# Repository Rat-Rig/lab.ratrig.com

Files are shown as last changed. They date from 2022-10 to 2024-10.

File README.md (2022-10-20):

# lab.ratrig.com

# What is the Rat Rig Lab?
Through the Rat Rig Lab, we share designs and ideas which fall into the following categories:

## Official Mods
Sometimes we need a particular part which we design internally. An example being an IEC socket mount which bolts onto an aluminium 3030 extrusion. These parts are developed but do not belong to any particular product we provide.

This section will serve as a home to all of those designs, so that members of the community can use them if they find the need. We provide both STEP and STL files for each, ready to be printed or added into your own mods.

## Upcoming & Prototype Products
From prototypes early in the development process, to designs nearing to official announcement and release. This section houses projects which we aim to make commercially available.

## Non-commercial Designs
The research and development process does not always result in a product that is commercially viable at the time. This section contains those designs which did not become a product we currently sell, but that we may revisit in the future.

We share and document these designs, as well as the ideas and timelines behind them in this section. You can also find CAD models and the bill of materials should someone wish to build the design for themselves.

### Discontinued Products
Products are sometimes superseded with new and improved versions, or simply no longer sell and are discontinued. Here you can find products which fall into these categories. We provide the CAD models, and the full bill of materials, so that these designs are never lost.

## CAD Repository
Most of the components we use in our CAD models are modelled in-house. This section is a repository of those CAD models which are available for the community to use in their own designs.

By using our official models, you can be assured that the design you create will match the product you can purchase.

# License
  

Unless specified otherwise, all content published on the Rat Rig Lab is licensed under the <a rel="license" href="http://creativecommons.org/licenses/by-nc-sa/4.0/">Creative Commons Attribution-NonCommercial-ShareAlike 4.0 International License</a>

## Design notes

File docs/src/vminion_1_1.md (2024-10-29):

---
title: V-Minion 1.1 Alpha
hide:
  - navigation
---
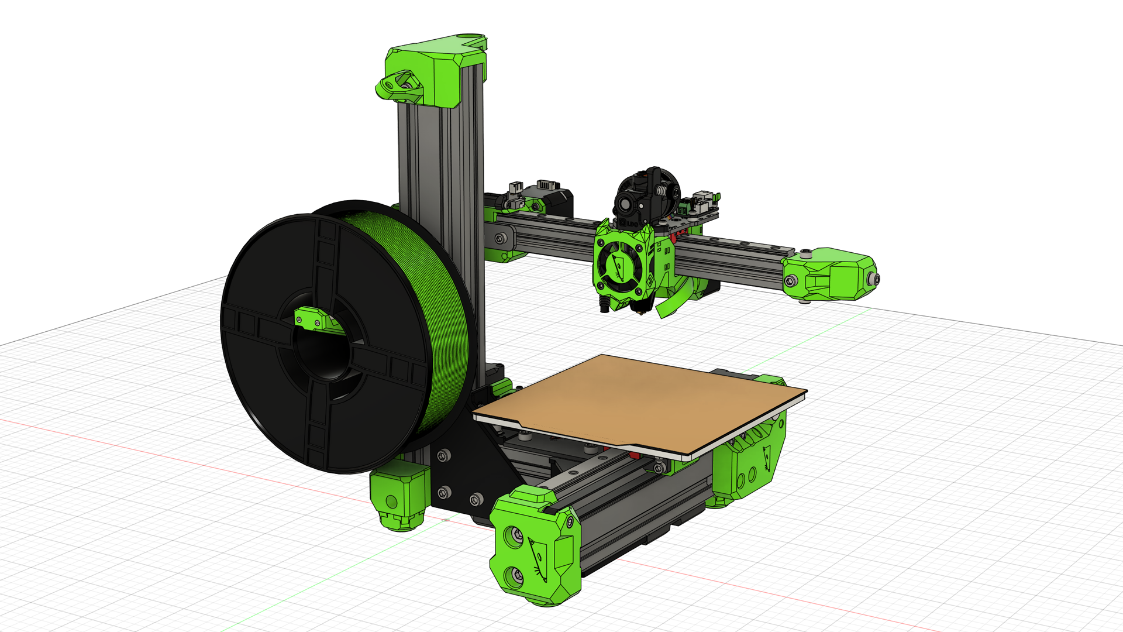
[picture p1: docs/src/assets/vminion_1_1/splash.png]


## About the V-Minion 1.1 Alpha
The V-Minion 1.1 was developed as an upgrade to the original V-Minion 1.0 design. It was intended to be an incremental update, rather than a full redesign. It improved upon the original in several ways:

- Removal of the external electronics enclosure, integrating them onto the V-Minion frame in a fully printed enclosure
- Addition of electronics cooling on the new enclosure
- Support for the BigTreeTech SKRat V1.0 motherboard
- Updated toolhead design, based upon the Rat Rig toolhead featured on the V-Core 3.1 and V-Core 4.0
- Improved routing and support of the bed cables
- Integrated lead screw decoupler on the Z-axis

### Kinematics
The V-Minion uses standard Cartesian kinematics. Unofficially these are often referred to as "bed slingers", as the print bed (and as such the print itself) moves in the Y direction during operation. As the Z-axis is only supported at one end, the V-Minion is considered to be a cantilevered design.

## Development Timeline
> 29/10/2024 - Added non-toolboard variant of the toolhead
> 15/10/2024 - Published to Rat Rig Lab

## Gallery
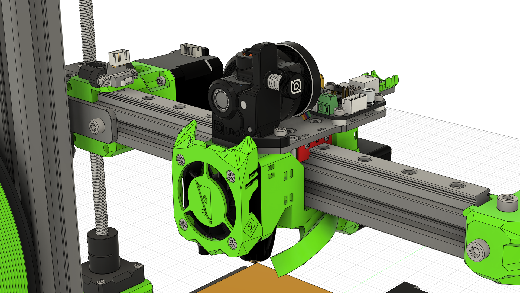
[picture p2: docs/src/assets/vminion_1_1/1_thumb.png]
{ target=_blank }
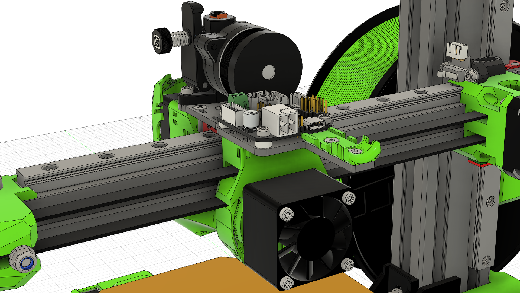
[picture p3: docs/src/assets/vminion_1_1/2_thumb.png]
{ target=_blank }
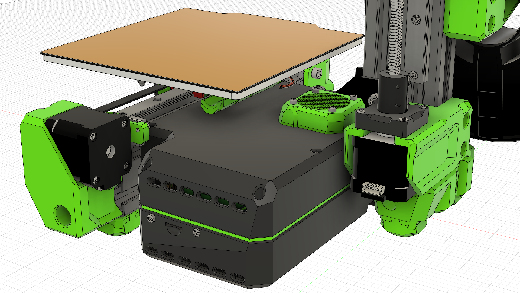
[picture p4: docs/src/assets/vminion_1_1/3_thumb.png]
{ target=_blank }
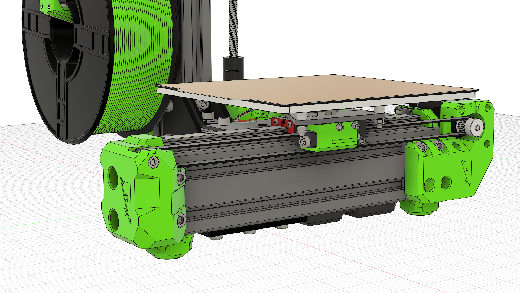
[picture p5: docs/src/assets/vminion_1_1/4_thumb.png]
{ target=_blank }

## CAD
[:material-file-cad-box: Rat Rig V-Minion 1.1 Alpha CAD](https://a360.co/48ehnFa){: .md-button .md-button--primary target=_blank } [:material-file-cad-box: Non-Toolboard Toolhead CAD](https://a360.co/3YEu60D){: .md-button .md-button--primary target=_blank }

## Bill of Materials
!!! attention "BOM Unavailable"
    At this time, no BOM is provided for the V-Minion 1.1. Please use the provided CAD model instead.

## License

Unless specified otherwise, all content published on the Rat Rig Lab is licensed under the <a rel="license" href="http://creativecommons.org/licenses/by-nc-sa/4.0/">Creative Commons Attribution-NonCommercial-ShareAlike 4.0 International License</a>

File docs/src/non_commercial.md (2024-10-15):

---
title: Non-Commercial Designs
hide:
  - navigation
---

## 3D Printers
### V-Cast 1.5
{{ rr_build_project_entry(
  "vcast_1_5",
  "Non-commercial", 
  "The V-Cast 1.5 was developed as an upgrade to the original V-Cast 1.0 design. It was intended to be an incremental update, improving upon certain areas, rather than being a full redesign.
  
  Due to the original V-Cast 1.0 being discontinued, this update never saw the light of day as a commercial product."
)}}

### V-Core 3.1 "Beast" Enclosure
{{ rr_build_project_entry(
  "vc31_beast_enclosure",
  "Non-commercial", 
  "This prototype was created during the development of the 2.0 enclosure for the V-Core 3.1. The design goal was to create an enclosure which only needed regular square panels, which would be cheaper and easier to acquire.
  
  Ultimately this resulted in several issues with machine maintenance, and as such was not chosen for the enclosure design."
)}}

### V-Minion 1.1 Alpha
{{ rr_build_project_entry(
  "vminion_1_1",
  "Non-commercial", 
  "The V-Minion 1.1 was intended to be an incremental upgrade to the original V-Minion 1.0 design. The goal was to integrate the electronics onto the V-Minion frame, as well as support a variant of the Rat Rig toolhead."
)}}

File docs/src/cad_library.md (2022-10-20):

---
title: CAD Library
hide:
  - navigation
---
<style type="text/css" rel="stylesheet">
  thead th:empty {
      border: thin solid red !important;
      display: none;
  }
</style>

!!! attention "Downloading CAD library models"
    To download a CAD model, please right click on the associated image below and choose "Save link as..." from the menu

## Components
{{ rr_cad_repo_build("components") }}

## Electronics
{{ rr_cad_repo_build("electronics") }}

## Extrusions
### 20 Series V-Slot
{{ rr_cad_repo_build("extrusions/20_series", False) }}

### 30 Series T-Slot
{{ rr_cad_repo_build("extrusions/30_series", False) }}

### 40 Series T-Slot
{{ rr_cad_repo_build("extrusions/40_series", False) }}

## Linear Rails
### MGN12
{{ rr_cad_repo_build("linear_rails/mgn12") }}

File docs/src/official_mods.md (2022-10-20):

---
title: Official Modifications
hide:
  - navigation
---
<style type="text/css" rel="stylesheet">
  thead th:empty {
      border: thin solid red !important;
      display: none;
  }
</style>

Sometimes we need a particular part which we design and use internally, but they do not belong to any particular product. A good example is an IEC socket mount which bolts onto an aluminium 3030 extrusion. Below we share these parts, and other modifications we develop, so that members of the community can use them if they find the need.

We provide both STEP and STL files, ready to be printed or added into your own CAD models.

### 3D Printable STLs
!!! attention "Downloading STL or STEP files"
    To download the STL or STEP files, please right click on the appropriate download link below and choose "Save link as..."

{{ rr_stl_repo_build() }}

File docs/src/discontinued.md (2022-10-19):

---
title: Discontinued Products
hide:
  - navigation
---

## 3D Printers
### V-Cast 1.0
{{ rr_build_project_entry(
  "vcast_1_0",
  "Discontinued", 
  "The V-Cast 1.0 is a premium Cartesian 3D printer design. Created to be rigid and strong, allowing fast printing without sacrificing quality.
  
  Designed to be capable of driving one or two extruders independently (also known as IDEX), allowing for multi-colour or multi-material prints."
)}}

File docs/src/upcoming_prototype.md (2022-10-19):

---
title: Upcoming & Prototype Products
hide:
  - navigation
---
## 3D Printers
### V-Core 3.1 IDEX
{{ rr_build_project_entry(
  "vc31_idex",
  "Prototype", 
  "The IDEX (or Independent Dual Extruder) version of the V-Core 3.1 was designed, in part, to fill the gap left by the discontinuation of the Rat Rig V-Cast.
  
  This variant features a reduced build volume which allows the external dimensions of the machine to match the non-IDEX counterpart."
)}}

### V-Core 3.1 IDEX "Wide Boy"
{{ rr_build_project_entry(
  "vc31_idex_wide",
  "Prototype", 
  "The IDEX (or Independent Dual Extruder) version of the V-Core 3.1 was designed, in part, to fill the gap left by the discontinuation of the Rat Rig V-Cast.
  
  This variant features a wider frame (unofficially dubbed the wide boy) which maintains the original print volume compared to the non-IDEX version."
)}}

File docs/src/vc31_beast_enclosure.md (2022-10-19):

---
title: V-Core 3.1 "Beast" Enclosure
hide:
  - navigation
---
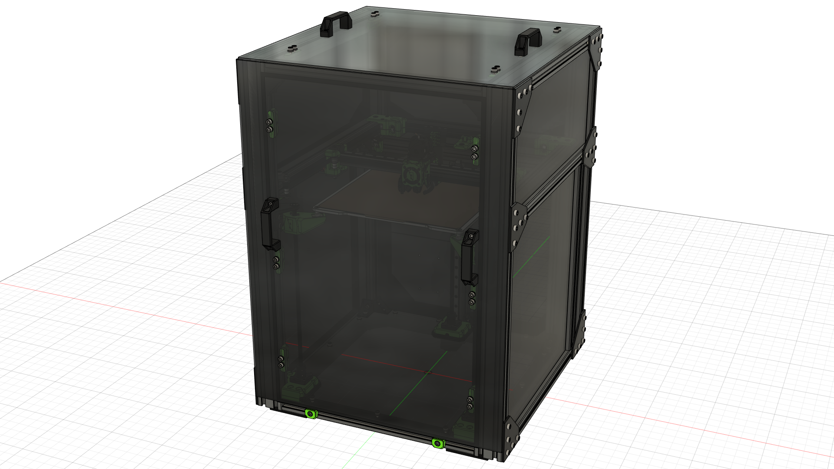
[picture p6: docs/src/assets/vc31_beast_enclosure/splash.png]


## About the V-Core 3.1 "Beast" Enclosure
This prototype was created during the development of the 2.0 enclosure for the V-Core 3.1. The design goal was to create an enclosure which only needed regular square panels, which would be cheaper and easier to acquire.

The design was ultimately abandoned due to multiple issues with machine maintenance when the panels are installed in such a way:

- Removing any of the side panels required partial disassembly of the machine frame, which was likely to cause the CoreXY system to need realignment
- The width of the frame increased by 60mm due to the use of 3060 extrusions on the sides
- The weight of the frame increased considerably due to the requirement of 3060 extrusions in various places

Ultimately, due to the issues mentioned above, this design was abandoned in favour of one which used panels screwed to the frame.

## Development Timeline
> 11/10/2022 - Added to Rat Rig Lab  
> 21/07/2022 - Prototype design complete  
> 18/07/2022 - Prototyping

## Gallery
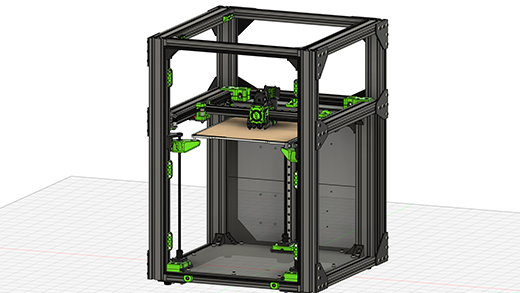
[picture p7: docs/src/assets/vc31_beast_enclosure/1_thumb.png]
{ target=_blank }
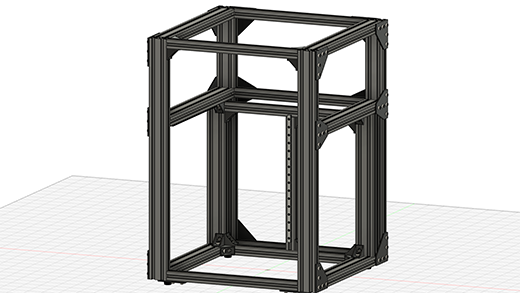
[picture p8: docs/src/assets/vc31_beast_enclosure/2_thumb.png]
{ target=_blank }
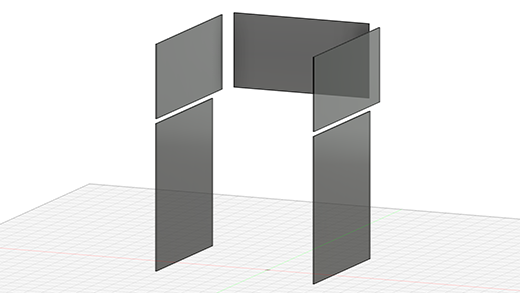
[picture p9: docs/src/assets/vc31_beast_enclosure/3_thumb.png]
{ target=_blank }
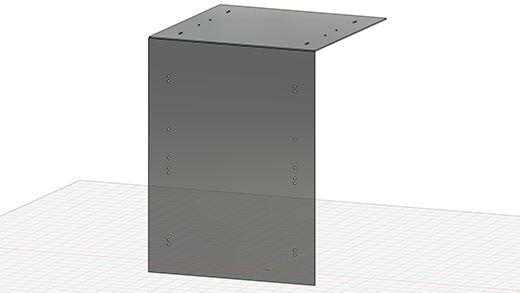
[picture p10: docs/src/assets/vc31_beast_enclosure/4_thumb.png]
{ target=_blank }

## CAD
[:material-file-cad-box: Click here to view the CAD on the Rat Rig Fusion 360 viewer](https://a360.co/3Tad6do){: .md-button .md-button--primary target=_blank }

## Bill of Materials
!!! attention "BOM Limitations"
    The bill of materials below is based upon a full machine build with a 300x300x300 print volume.
    
    Components required to build the EVA3 tool head are not listed.
{{ hardware_bom("assets/vc31_beast_enclosure/bom.csv") }}

## Printed Parts
!!! attention "EVA3 Printed Parts"
    Printed parts required to build the EVA3 tool head are not listed below.
{{ printed_parts_bom_minimal("assets/vc31_beast_enclosure/printed_parts.csv") }}

## License

Unless specified otherwise, all content published on the Rat Rig Lab is licensed under the <a rel="license" href="http://creativecommons.org/licenses/by-nc-sa/4.0/">Creative Commons Attribution-NonCommercial-ShareAlike 4.0 International License</a>

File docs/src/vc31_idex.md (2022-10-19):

---
title: V-Core 3.1 IDEX
hide:
  - navigation
---
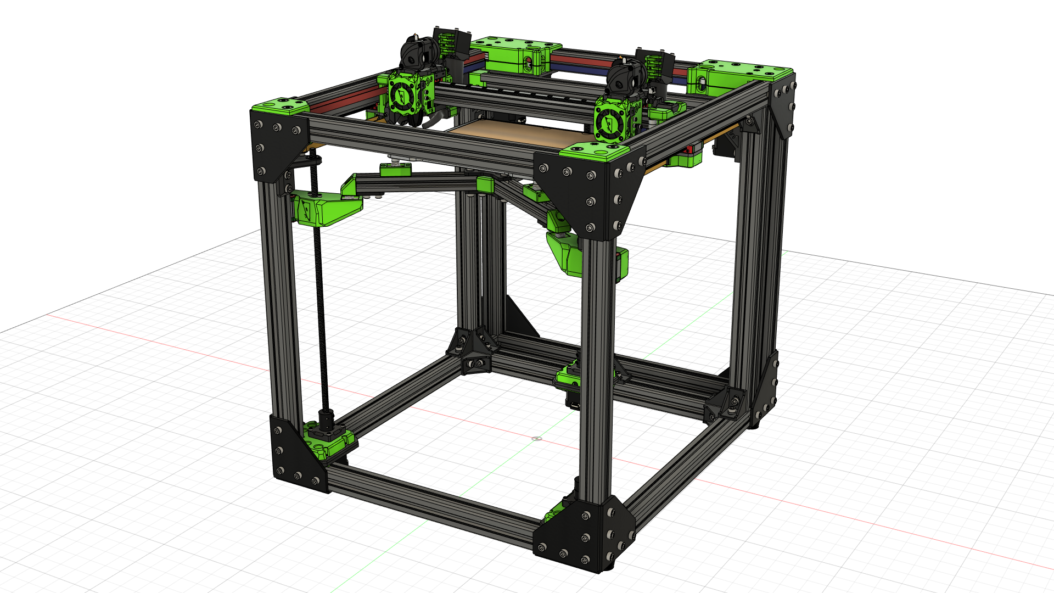
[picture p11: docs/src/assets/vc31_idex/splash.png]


## About the V-Core 3.1 IDEX
The "IDEX" (or Independent Dual Extruder) version of the V-Core 3.1 was designed, in part, to fill the gap left by the discontinuation of the Rat Rig V-Cast.

### Variants
Due to the space constraints caused by requiring two EVA tool heads, the IDEX V-Core 3.1 was developed into two separate designs. This page details the design which maintains the same external dimensions as the existing V-Core 3 sizes. This comes at the expense of a reduced build volume in X and Y. The alternate design, unofficially dubbed the "wide boy", increases the frame size in the X-axis direction, but maintains the original print volume.

Details of the "wide boy" design can be found on its own page [accessed by clicking here](/vc31_idex_wide/).

### Kinematics
Adaptions to the kinematics were required to make IDEX work on the V-Core 3.1. The kinematics chosen are widely known as "Dual Markforge" kinematics. Two NEMA17 new stepper motors are used to drive the Y-axis (one per side), and then the existing A/B NEMA17 steppers are used to drive the two tool heads.

## Development Timeline
> 11/10/2022 - Published to Rat Rig Lab  
> 04/07/2022 - V-Core 3.1 IDEX prototype design complete  
> 14/04/2022 - Prototyping for V-Core 3.1  
> 24/01/2021 - V-Core 3.0 IDEX prototype design complete  
> 30/09/2021 - Prototyping

## Known issues
> The Y-axis endstop has an interference issue with the Y-axis IDEX belts

## Gallery
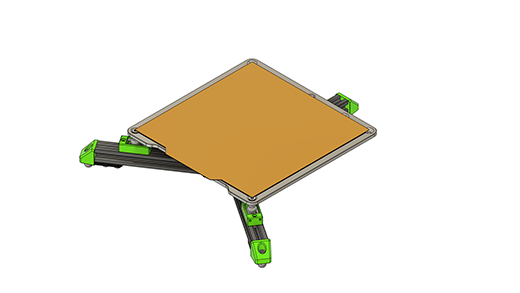
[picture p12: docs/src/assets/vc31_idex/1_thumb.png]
{ target=_blank }
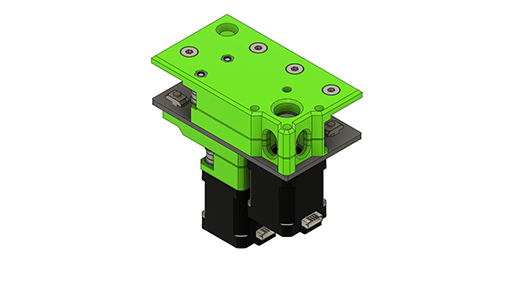
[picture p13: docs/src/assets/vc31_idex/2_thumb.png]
{ target=_blank }
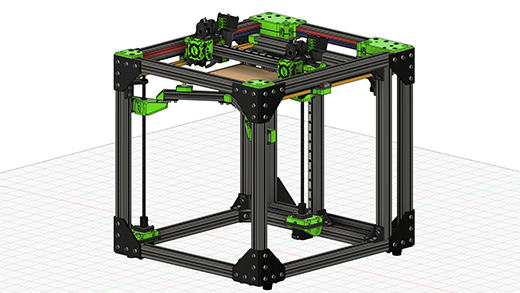
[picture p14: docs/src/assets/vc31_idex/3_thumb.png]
{ target=_blank }
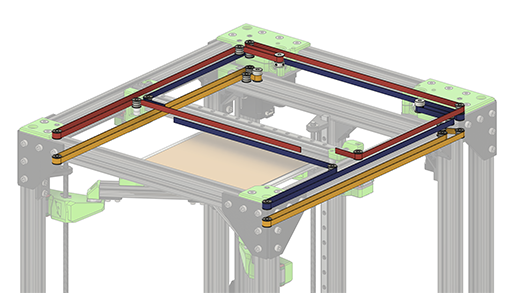
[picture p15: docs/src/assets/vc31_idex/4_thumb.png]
{ target=_blank }

## CAD
[:material-file-cad-box: Click here to view the CAD on the Rat Rig Fusion 360 viewer](https://a360.co/3SVh2OY){: .md-button .md-button--primary target=_blank }

## Bill of Materials
!!! attention "BOM Limitations"
    The bill of materials below is based upon a full machine build with a 300x300x300 print volume.
    
    Components required to build the EVA3 tool heads are not listed.
{{ hardware_bom("assets/vc31_idex/bom.csv") }}

## Printed Parts
!!! attention "EVA3 & IDEX Printed Parts"
    EVA3 does not currently support IDEX, therefore modified EVA3 back printed parts are provided in the CAD (eva3_idex_back_x1 & eva3_idex_back_x2).

    Printed parts required to build the EVA3 tool heads are not listed below.
{{ printed_parts_bom_minimal("assets/vc31_idex/printed_parts.csv") }}

## License

Unless specified otherwise, all content published on the Rat Rig Lab is licensed under the <a rel="license" href="http://creativecommons.org/licenses/by-nc-sa/4.0/">Creative Commons Attribution-NonCommercial-ShareAlike 4.0 International License</a>

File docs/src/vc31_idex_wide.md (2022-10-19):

---
title: V-Core 3.1 IDEX "Wide Boy"
hide:
  - navigation
---
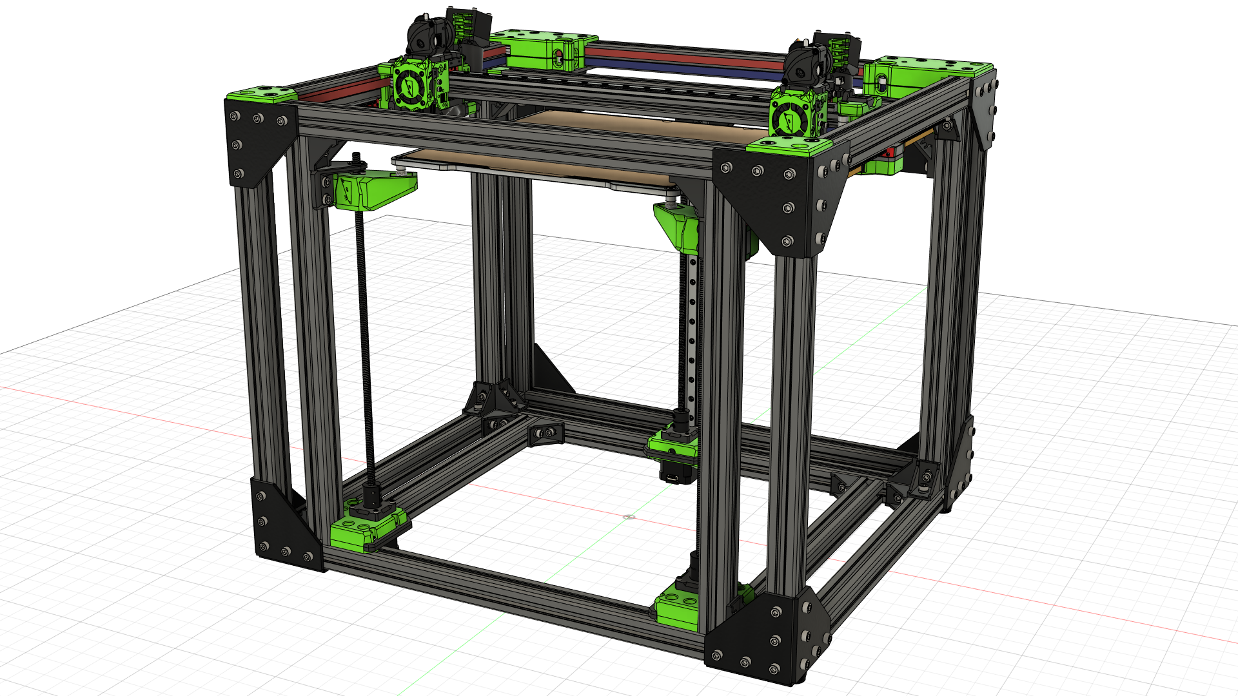
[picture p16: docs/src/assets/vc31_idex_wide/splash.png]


## About the V-Core 3.1 IDEX "Wide Boy"
The "IDEX" (or Independent Dual Extruder) version of the V-Core 3.1 was designed, in part, to fill the gap left by the discontinuation of the Rat Rig V-Cast.

### Variants
Due to the space constraints caused by requiring two EVA tool heads, the IDEX V-Core 3.1 was developed into two separate designs. This page details the "wide boy" design which increases the size of the frame in the X-axis direction. This allows for the full print volume of the original, although has the downside of being a physically larger machine. The alternate design, which features the same external dimensions as a non-IDEX V-Core 3, uses a smaller print bed and a bed subframe.

Details of the alternate design can be found on its own page [accessed by clicking here](/vc31_idex/).

### Kinematics
Adaptions to the kinematics were required to make IDEX work on the V-Core 3.1. The kinematics chosen are widely known as "Dual Markforge" kinematics. Two NEMA17 new stepper motors are used to drive the Y-axis (one per side), and then the existing A/B NEMA17 steppers are used to drive the two tool heads.

## Development Timeline
> 11/10/2022 - Published to Rat Rig Lab  
> 04/07/2022 - V-Core 3.1 IDEX prototype design complete  
> 14/04/2022 - Prototyping for V-Core 3.1  
> 24/01/2021 - V-Core 3.0 IDEX prototype design complete  
> 30/09/2021 - Prototyping

## Known issues
> 1 - The Y-axis endstop has an interference issue with the Y-axis IDEX belts  
> 2 - The front lead screw constraints are customised due to an interference issue with the stock design

## Gallery
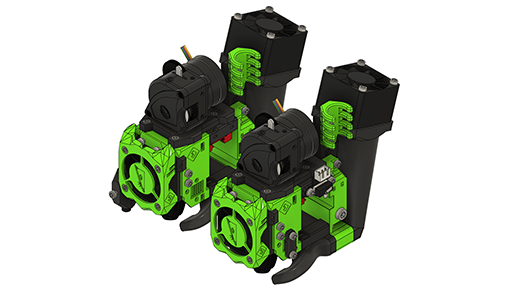
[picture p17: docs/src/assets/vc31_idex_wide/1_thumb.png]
{ target=_blank }
{ target=_blank }
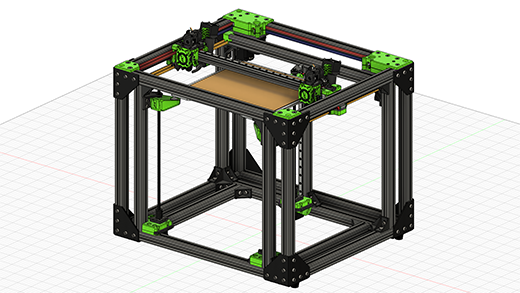
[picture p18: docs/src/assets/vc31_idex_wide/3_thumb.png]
{ target=_blank }
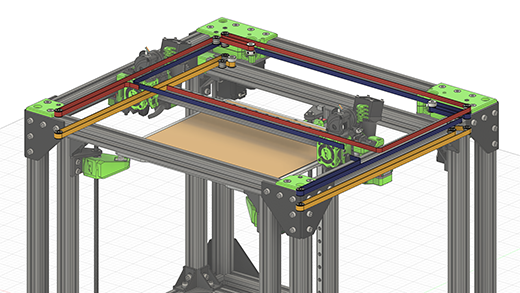
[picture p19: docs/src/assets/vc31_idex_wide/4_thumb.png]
{ target=_blank }

## CAD
[:material-file-cad-box: Click here to view the CAD on the Rat Rig Fusion 360 viewer](https://a360.co/3CtRwJU){: .md-button .md-button--primary target=_blank }

## Bill of Materials
!!! attention "BOM Limitations"
    The bill of materials below is based upon a full machine build with a 300x300x300 print volume.
    
    Components required to build the EVA3 tool heads are not listed.
{{ hardware_bom("assets/vc31_idex_wide/bom.csv") }}

## Printed Parts
!!! attention "EVA3 & IDEX Printed Parts"
    EVA3 does not currently support IDEX, therefore modified EVA3 back printed parts are provided in the CAD (eva3_idex_back_x1 & eva3_idex_back_x2).

    Printed parts required to build the EVA3 tool heads are not listed below.
{{ printed_parts_bom_minimal("assets/vc31_idex_wide/printed_parts.csv") }}

## License

Unless specified otherwise, all content published on the Rat Rig Lab is licensed under the <a rel="license" href="http://creativecommons.org/licenses/by-nc-sa/4.0/">Creative Commons Attribution-NonCommercial-ShareAlike 4.0 International License</a>

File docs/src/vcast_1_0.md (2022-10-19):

---
title: V-Cast 1.0
hide:
  - navigation
---
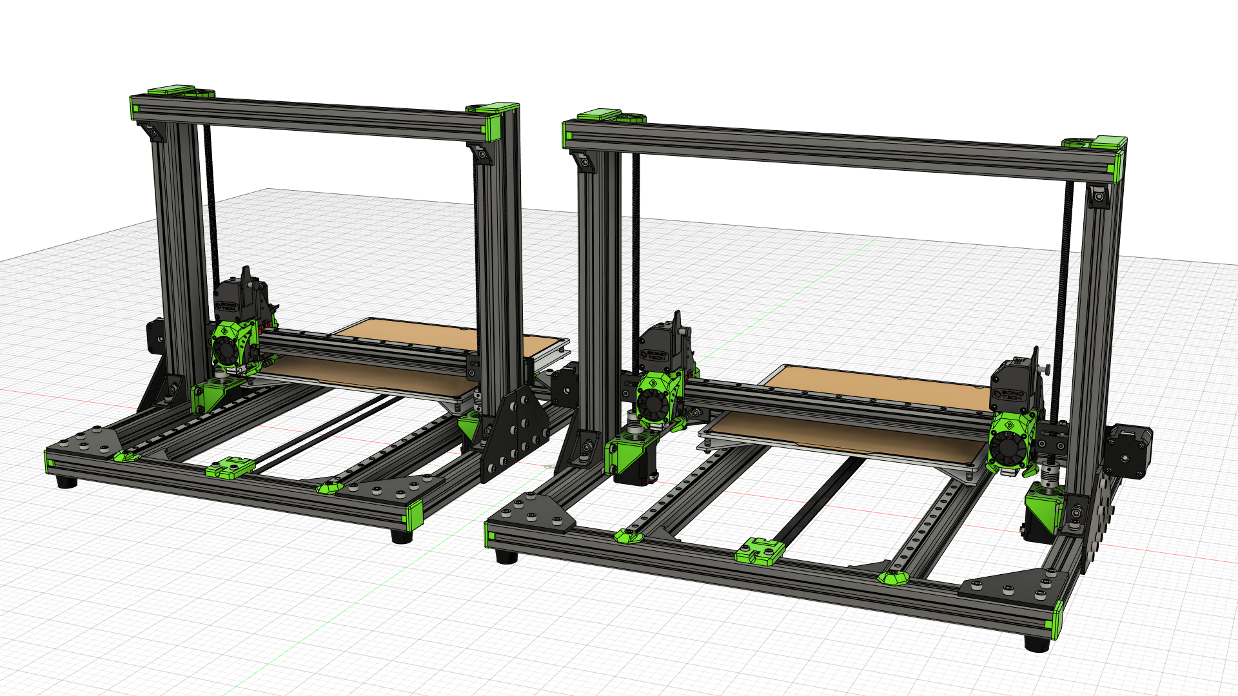
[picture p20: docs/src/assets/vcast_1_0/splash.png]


## About the V-Cast 1.0

### Variants
The V-Cast features two variants, both of which can be used with either a single extruder, or a pair of extruders for IDEX.

The wider frame, unofficially dubbed the "wide boy", was created to allow the extruder(s) to completely leave the print volume when not in use. This is important for the IDEX configuration as it allows both extruders to reach all points on the print bed, thus enabling the full print volume in multi-colour or multi-material prints.

### Kinematics
The V-Cast uses standard Cartesian kinematics. Unofficially these are often referred to as "bed slingers", as the print bed (and as such the print itself) moves in the Y direction during operation.

## Development Timeline
> 11/10/2022 - Published to Rat Rig Lab  
> 09/02/2022 - Discontinued  
> 01/09/2020 - Launched  
> 26/05/2020 - Beta Testing  
> xx/xx/2020 - V-Cast 1.0 prototype design complete  
> xx/xx/2020 - Prototyping

## Gallery
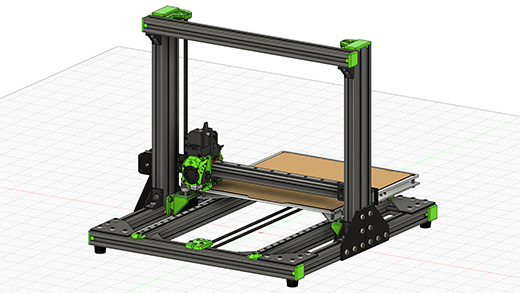
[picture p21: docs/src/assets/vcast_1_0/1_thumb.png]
{ target=_blank }
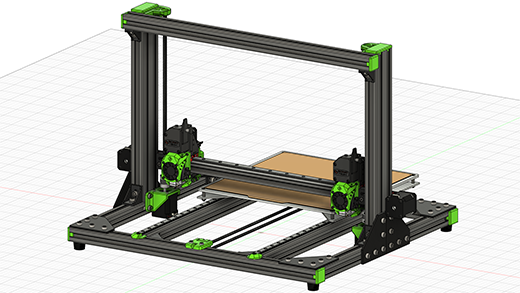
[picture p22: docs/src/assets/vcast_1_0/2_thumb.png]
{ target=_blank }

## CAD
[:material-file-cad-box: Rat Rig V-Cast v1.0 CAD](https://a360.co/3TbjzVw){: .md-button .md-button--primary target=_blank } [:material-file-cad-box: Rat Rig V-Cast v1.0 "Wide Boy" CAD](https://a360.co/3Tpx1Vi){: .md-button .md-button--primary target=_blank }

## Bill of Materials
!!! attention "BOM Limitations"
    The bill of materials lists only the parts required for the mechanical build. Electronics
    Components required to build the EVA2 tool heads are not listed.

### V-Cast 1.0 Standard Frame
{{ hardware_bom("assets/vcast_1_0/bom.csv") }}

### V-Cast 1.0 "Wide Boy" Frame
{{ hardware_bom("assets/vcast_1_0/bom_wide.csv") }}

### V-Cast 1.0 IDEX Additions
{{ hardware_bom("assets/vcast_1_0/bom_idex_additions.csv") }}

## Printed Parts
!!! attention "EVA2 Printed Parts"
    Printed parts required to build the EVA2 tool heads are not listed below.
{{ printed_parts_bom_minimal("assets/vcast_1_0/printed_parts.csv") }}

## License

Unless specified otherwise, all content published on the Rat Rig Lab is licensed under the <a rel="license" href="http://creativecommons.org/licenses/by-nc-sa/4.0/">Creative Commons Attribution-NonCommercial-ShareAlike 4.0 International License</a>

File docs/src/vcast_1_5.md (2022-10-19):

---
title: V-Cast 1.5
hide:
  - navigation
---
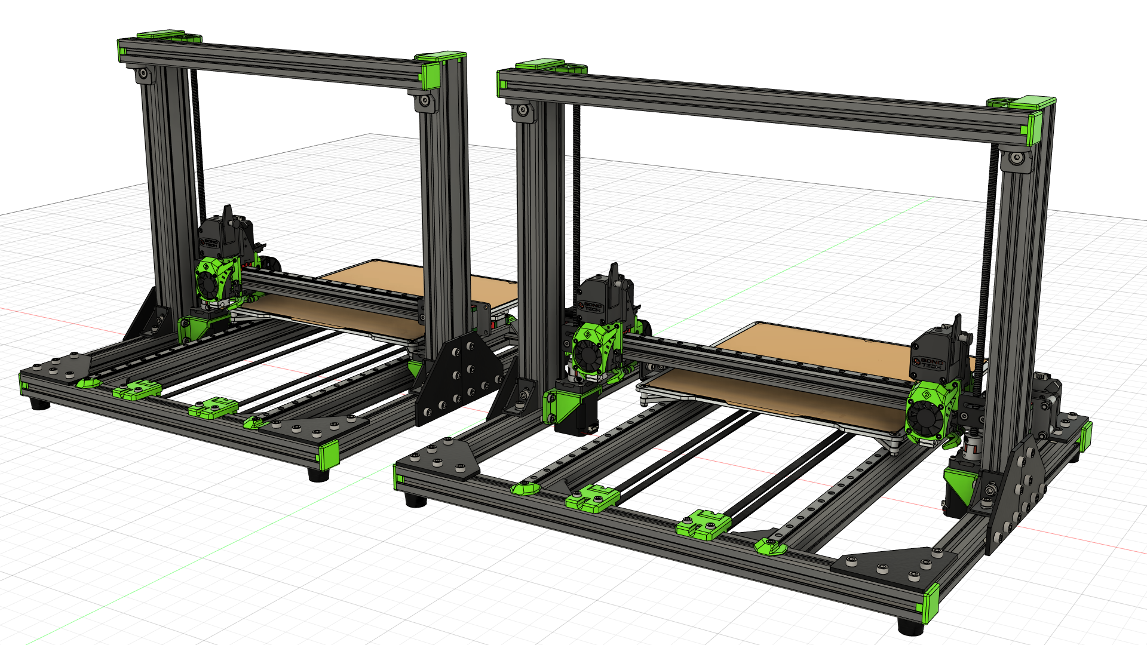
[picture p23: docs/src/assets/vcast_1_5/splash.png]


## About the V-Cast 1.5
The V-Cast 1.5 was developed as an upgrade to the original V-Cast 1.0 design. It was intended to be an incremental update, rather than a full redesign. It improved upon the original in several ways:

- Complete redesign of the X-axis transmission for both single and IDEX configurations
- Relocated the X and U-axis motors to be inside the frame, decreasing the total width of the machine by 62mm in IDEX
- New three point rigid bed mounting, using the same machined bed plates as the V-Core 3
- Updated Y-axis carriage, which is stronger, yet lighter
- Addition of a second Y-axis motor for additional torque when moving the bed
- Addition of axial thrust bearings & pillow blocks to both Z-axis motor assemblies

### Variants
The V-Cast 1.5 features the same two variants as the V-Cast 1.0, both of which can be used with either a single extruder, or a pair of extruders for IDEX.

The wider frame, unofficially dubbed the "wide boy", was created to allow the extruder(s) to completely leave the print volume when not in use. This is important for the IDEX configuration as it allows both extruders to reach all points on the print bed, thus enabling the full print volume in multi-colour or multi-material prints.

### Kinematics
The V-Cast uses standard Cartesian kinematics. Unofficially these are often referred to as "bed slingers", as the print bed (and as such the print itself) moves in the Y direction during operation.

## Development Timeline
> 11/10/2022 - Published to Rat Rig Lab  
> 08/02/2022 - V-Cast 1.5 prototype design complete  
> 22/09/2021 - Prototyping

## Gallery
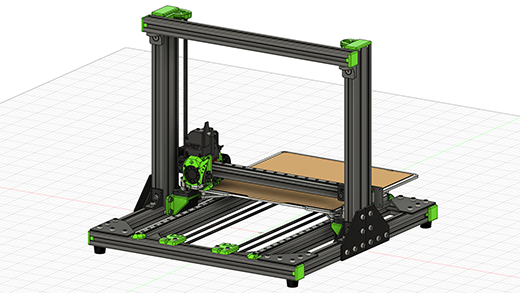
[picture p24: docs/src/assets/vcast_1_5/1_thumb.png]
{ target=_blank }
{ target=_blank }

## CAD
[:material-file-cad-box: Rat Rig V-Cast v1.5 CAD](https://a360.co/3S9SQY0){: .md-button .md-button--primary target=_blank } [:material-file-cad-box: Rat Rig V-Cast v1.5 "Wide Boy" CAD](https://a360.co/3ySI41x){: .md-button .md-button--primary target=_blank }

## Bill of Materials
!!! attention "BOM Limitations"
    The bill of materials lists only the parts required for the mechanical build. Electronics
    Components required to build the EVA2 tool heads are not listed.

### V-Cast 1.5 Standard Frame
{{ hardware_bom("assets/vcast_1_5/bom.csv") }}

### V-Cast 1.5 "Wide Boy" Frame
{{ hardware_bom("assets/vcast_1_5/bom_wide.csv") }}

## Printed Parts
!!! attention "EVA2 Printed Parts"
    Printed parts required to build the EVA2 tool heads are not listed below.
{{ printed_parts_bom_minimal("assets/vcast_1_5/printed_parts.csv") }}

## License

Unless specified otherwise, all content published on the Rat Rig Lab is licensed under the <a rel="license" href="http://creativecommons.org/licenses/by-nc-sa/4.0/">Creative Commons Attribution-NonCommercial-ShareAlike 4.0 International License</a>

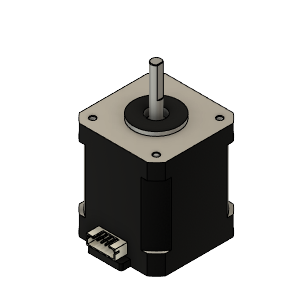
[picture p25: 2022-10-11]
docs/src/cad/electronics/HW1078EC-Nema 17 Stepper Motor - 48mm - 1.8degree, 76oz-in.png

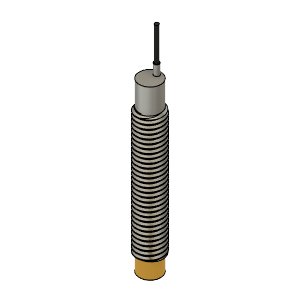
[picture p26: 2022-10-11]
docs/src/cad/electronics/HW2819EC-Inductive Probe 5V - M8.png

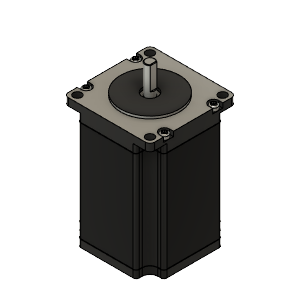
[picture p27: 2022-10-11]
docs/src/cad/electronics/HW1462EC-Nema 23 Stepper Motor - High Torque - 1.8deg, 345oz-in.png

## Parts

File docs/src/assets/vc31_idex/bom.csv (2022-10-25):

 | SKU |  |  | Product Name
 | IDEX Assembly - 300x300x300 |  |  | IDEX Assembly - 300x300x300
 |  |  |  | 11/10/2022 14:32
 | B.O.M.
QTY | SKU | Length (mm) | Tap | Item Name | Cost (unit) | Cost Line
QTY | SKU | Length (mm) | Tap | Item Name
1 | HW306BRC | 400 |  | T-Slot 3030 - Black - 400mm
1 | HW306BRC | 420 |  | T-Slot 3030 - Black - 420mm
5 | HW306BRC | 440 |  | T-Slot 3030 - Black - 440mm
2 | HW306BRC | 450 |  | T-Slot 3030 - Black - 450mm
4 | HW306BRC | 505 |  | T-Slot 3030 - Black - 505mm
4 | HW306BRC | 510 |  | T-Slot 3030 - Black - 510mm
2 | HW201BRC | 166 |  | V-Slot 2020 - Black - 166mm
1 | HW201BRC | 185 |  | V-Slot 2020 - Black - 185mm
1 | HW201BRC | 422 |  | V-Slot 2020 - Black - 422mm
2 |  |  |  | 3060 90 Degree Corner
19 | HW1018NC |  |  | Aluminium Spacer - 6mm
2 | HW1019NC |  |  | Aluminium Spacer - 9mm
18 | HW2948WC |  |  | Ball Bearing - 695ZZ
3 | HW1309WC |  |  | Ball Bearing - F688ZZ
36 | HW2947WC |  |  | Ball Bearing - F695ZZ
1 | HW2954PC |  |  | Bed Plate - Cast tooling plate - Pre-Machined - 229x229x5mm
38 | HW1502SC |  |  | Cap Head Screw M3x8
98 | HW1292SC |  |  | Cap Head Screw M3x12
20 | HW1866SC |  |  | Cap Head Screw M3x18
8 | HW1504SC |  |  | Cap Head Screw M3x20
10 | HW1868SC |  |  | Cap Head Screw M3x35
4 | HW1869SC |  |  | Cap Head Screw M3x40
2 | HW0000SC |  |  | Cap Head Screw M4x40
22 | HW1285SC |  |  | Cap Head Screw M5x10
3 | HW1202SC |  |  | Cap Head Screw M5x12
6 | HW2110SC |  |  | Cap Head Screw M5x18
3 | HW1060SC |  |  | Cap Head Screw M5x35
2 | HW2138SC |  |  | Cap Head Screw M5x40
4 | HW2140SC |  |  | Cap Head Screw M5x55
2 | HW2957SC |  |  | Cap Head Screw M5x65
2 | HW2958SC |  |  | Cap Head Screw M5x70
141 | HW1836SC |  |  | Cap Head Screw M6x12
4 | HW2827SC |  |  | Cap Head Screw M6x16
9 | HW1870SC |  |  | Cap Head Screw M6x20
10 | HW1916BC |  |  | Cast 90 Degree Corner Bracket for 3030 - 6 Slot - Black
12 | HW1874SC |  |  | Countersink Screw M3x12
3 | HW2349SC |  |  | Countersink Screw M5x16
12 | HW2173SC |  |  | Countersink Screw M6x14
3 | HW2990GC |  |  | Coupler - Rigid Type - Black 25x20mm - 5mm to 8mm
12 | HW2126GC |  |  | Dowel Pin - 3x35mm
1 | HW2954GC |  |  | FlexPlate Set - Powder coated PEI 210x210mm
26 | HW1251NC |  |  | Hex Locking Nut - M3
2 | HW1374NC |  |  | Hex Locking Nut - M4
13 | HW1039NC |  |  | Hex Locking Nut - M5
2 | HW2201PC |  |  | idler_plate_v1.0
20 | HW1915PC |  |  | Joining Plate for 3030 - 90 Degree - Black Anodized
1 | HW2956EC |  |  | Keenovo 180x180 250W Silicone Heater Pad
3 | HW2191SC |  |  | Lead Screw - TR8*4 Metric Acme Lead Screw - 380mm
3 | HW2915GC |  |  | Leadscrew Nut - POM - TR8*4
2 | HW2353GC | 350 |  | Linear Rail - MGN12 350mm + MGN12C carriage
3 | HW2036GC | 400 |  | Linear Rail - MGN12 400mm + MGN12C carriage
1 |  | 400 |  | Linear Rail - MGN12 400mm + 2 x MGN12C carriage
6 | HW2127GC |  |  | Magnet - 20x10x5mm - Two hole (M3 Countersink screws)
38 | HW1630NC |  |  | Mini Precision Shim - 8x5x1mm
7 | HW1078EC |  |  | Nema 17 Stepper Motor - 48mm - 1.8degree/step, 76oz-in
3 | HW2950WC |  |  | Rat Rig Bi-Material Lead Screw Decoupler
4 | HW2125GC |  |  | Rubber foot with metal insert - Heavy Duty - 28x22x16.5mm
6 | HW2128GC |  |  | Steel Ball - 12mm - Threaded M5
22 | HW1665NC |  |  | T-Nut - Drop In for 2020 - M3
76 | HW1821NC |  |  | T-Nut - Drop In for 3030 - M3
4 | HW1383NC |  |  | T-Nut - Drop In for 3030 - M5
166 | HW1361NC |  |  | T-Nut - Drop In for 3030 - M6
24 | HW1522NC |  |  | T-Nut - Square type for 2020 - M5
3 | HW2118WC |  |  | Thrust Bearing F8-16M
4 | HW1654WC |  |  | Timing Pulley - 2GT (2mm) - 20 Tooth - For 9mm Belt - 5mm Bore
3 |  |  |  | vc3_idex_bed_arm_plate
2 |  |  |  | vc3_idex_bed_joiner_plate
2 | HW3146PC |  |  | Rat Rig V-Core 3.1 - IDEX Motor Plate v1.0
2 | HW2949PC |  |  | VC3-XY_Joiner_Plate_v1.1
20 | HW1315NC |  |  | Washer Simple M5
20 | HW1314NC |  |  | Washer Simple M6

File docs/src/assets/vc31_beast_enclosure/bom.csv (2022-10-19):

 | SKU |  |  | Product Name
 | V-Core 3.1 Beast Enclosure |  |  | V-Core 3.1 Beast Enclosure
 |  |  |  | 19/10/2022 12:26
 | B.O.M.
QTY | SKU | Length (mm) | Tap | Item Name
1 | HW306BRC | 420 |  | T-SLOT 3030 - Black Anodized 1000mm
7 | HW306BRC | 440 |  | T-SLOT 3030 - Black Anodized 1000mm
2 | HW316BRC | 450 |  | T-SLOT 3060 - Black Anodized 1000mm
6 | HW316BRC | 505 |  | T-SLOT 3060 - Black Anodized 1000mm
4 | HW316BRC | 760 |  | T-SLOT 3060 - Black Anodized 1000mm
1 | HW201BRC | 422 |  | V-SLOT 2020 - Black Anodized 1000mm
2 | HW1016NC |  |  | Aluminium Spacer - 3mm
15 | HW1018NC |  |  | Aluminium Spacer - 6mm
12 | HW2948WC |  |  | Ball Bearing - 695ZZ
24 | HW2947WC |  |  | Ball Bearing - F695ZZ
3 | HW1309WC |  |  | Ball Bearing F688ZZ Flanged 8 x 16 x 5
1 | HW2198PC |  |  | Bed Plate - Cast tooling plate - Pre-Machined - 329*329*6mm
94 | HW1292SC |  |  | Cap Head Screw M3 (Single) (Length: 12mm)
12 | HW1866SC |  |  | Cap Head Screw M3 (Single) (Length: 18mm)
8 | HW1504SC |  |  | Cap Head Screw M3 (Single) (Length: 20mm)
10 | HW1868SC |  |  | Cap Head Screw M3 (Single) (Length: 35mm)
36 | HW1502SC |  |  | Cap Head Screw M3 (Single) (Length: 8mm)
5 | HW1285SC |  |  | Cap Head Screw M5 (Single) (Length: 10mm)
2 | HW1202SC |  |  | Cap Head Screw M5 (Single) (Length: 12mm)
5 | HW2110SC |  |  | Cap Head Screw M5 (Single) (Length: 18mm)
4 | HW2138SC |  |  | Cap Head Screw M5 (Single) (Length: 40mm)
2 | HW2074SC |  |  | Cap Head Screw M5 (Single) (Length: 45mm)
4 | HW2140SC |  |  | Cap Head Screw M5 (Single) (Length: 55mm)
241 | HW1836SC |  |  | Cap Head Screw M6 (Single) (Length: 12mm)
8 | HW2827SC |  |  | Cap Head Screw M6 (Single) (Length: 16mm)
9 | HW1870SC |  |  | Cap Head Screw M6 (Single) (Length: 20mm)
16 | HW1916BC |  |  | Cast 90 Degree Corner Bracket for 3030 - 6 Slot - Black
6 | HW1874SC |  |  | Countersink Screw M3 (Single) (Length: 12mm)
3 | HW2349SC |  |  | Countersink Screw M5 (Single) (Length: 16mm)
2 | HW2173SC |  |  | Countersink Screw M6 (Single) (Length: 14mm)
3 | HW2990GC |  |  | Coupler - Rigid Type - Black 25*20mm - 5mm to 8mm
6 | HW2126GC |  |  | Dowel Pin - 3.0mm x 35.0mm
1 | HW2685EC |  |  | Endstop Module - Horizontal Limit switch with 1mt cable and connector
1 | HW2943GC | 4500 |  | Foam (meter) - 1mm x 8mm x 1000mm - Adhesive 3M - EVA material
20 | HW1251NC |  |  | Hex Locking Nut - M3
11 | HW1039NC |  |  | Hex Locking Nut - M5
28 | HW1311NC |  |  | Hex Locking Nut - M6
16 | HW1915PC |  |  | Joining Plate for 3030 - 90 Degree - Black Anodized
6 | HW1914PC |  |  | Joining Plate for 3030 - T - Black Anodized
3 | HW2191SC |  |  | Lead Screw - TR8*4 Metric Acme Lead Screw - 380mm
3 | HW2915GC |  |  | Leadscrew Nut - POM - TR8*4
2 | HW2353GC |  |  | Linear Rail - MGN12 350mm + MGN12C carriage
4 | HW2036GC |  |  | Linear Rail - MGN12 400mm + MGN12C carriage
3 | HW2127GC |  |  | Magnet - 20 x 10 x 5mm - Two hole (M3 Countersink screws)
20 | HW2828GC |  |  | Magnet - Neodymium disc shape - 10mm x 4mm
20 | HW2828GC |  |  | Magnet - Neodymium disc shape - 10mm x 4mm
28 | HW1630NC |  |  | Mini Precision Shim - 8 x 5 x 1mm
5 | HW1078EC |  |  | Nema 17 Stepper Motor - 48mm - 1.8degree/step, 76oz-in
3 | HW2950WC |  |  | Rat Rig Bi-Material Lead Screw Decoupler
4 | HW3056PC |  |  | Rat Rig V-Core 3 - Enclosure v2.0 - Idler Plate v1.0
4 | HW2125GC |  |  | Rubber foot with metal insert - Heavy Duty - 28*22*16.5mm
3 | HW2128GC |  |  | Steel Ball - 12mm - Threaded M5
16 | HW1665NC |  |  | T-Nut - Drop In for 2020 - M3 (Single)
76 | HW1821NC |  |  | T-Nut - Drop In for 3030 - M3 (Single)
5 | HW1383NC |  |  | T-Nut - Drop In for 3030 - M5 (Single)
232 | HW1361NC |  |  | T-Nut - Drop In for 3030 - M6 (Single)
6 | HW1522NC |  |  | T-Nut - Square for 2020 - M5 (Single)
3 | HW2118WC |  |  | Thrust Bearing F8-16M
2 | HW1654WC |  |  | Timing Pulley - 2GT (2mm) - 20 Tooth - For 9mm Belt - 5mm Bore
2 | HW2202PC |  |  | V-Core 3.0 - MOTOR_PLATE_V1.0
2 | HW2949PC |  |  | V-Core 3.1 - XY_JOINER_PLATE_V1.1
4 | HW1555GC |  |  | V-Slot Door Handle
87 | HW1314NC |  |  | Washer Simple M6

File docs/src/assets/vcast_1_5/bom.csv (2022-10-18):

 | SKU |  |  | Product Name
 |  |  |  | Rat Rig V-Cast v1.5
 |  |  |  | 18/10/2022 14:09
 | B.O.M.
QTY | SKU | Length (mm) | Tap | Item Name
4 | HW306BRC | 480 |  | T-SLOT 3030 - Black Anodized 1000mm
3 | HW306BRC | 492 |  | T-SLOT 3030 - Black Anodized 1000mm
2 | HW316BRC | 400 |  | T-SLOT 3060 - Black Anodized 1000mm
1 | HW201BRC | 420 |  | V-SLOT 2020 - Black Anodized 1000mm
4 |  |  |  | Aluminium Spacer - 20mm
3 | HW1019NC |  |  | Aluminium Spacer - 9mm
2 | HW1021GC |  |  | Anti-Backlash Nut Block for 8mm Metric Acme Lead Screw TR8*8
1 | HW2198PC |  |  | Bed Plate - Cast tooling plate - Pre-Machined - 329*329*6mm
8 | HW1336SC |  |  | Button Head Screw M3 (Single) (Length: 8mm)
68 | HW1292SC |  |  | Cap Head Screw M3 (Single) (Length: 12mm)
8 | HW1866SC |  |  | Cap Head Screw M3 (Single) (Length: 18mm)
22 | HW1504SC |  |  | Cap Head Screw M3 (Single) (Length: 20mm)
4 | HW1868SC |  |  | Cap Head Screw M3 (Single) (Length: 35mm)
36 | HW1502SC |  |  | Cap Head Screw M3 (Single) (Length: 8mm)
26 | HW1202SC |  |  | Cap Head Screw M5 (Single) (Length: 12mm)
4 | HW2116SC |  |  | Cap Head Screw M5 (Single) (Length: 14mm)
5 | HW1054SC |  |  | Cap Head Screw M5 (Single) (Length: 20mm)
2 | HW1055SC |  |  | Cap Head Screw M5 (Single) (Length: 25mm)
4 | HW1060SC |  |  | Cap Head Screw M5 (Single) (Length: 35mm)
1 | HW1210SC |  |  | Cap Head Screw M5 (Single) (Length: 8mm)
60 | HW1836SC |  |  | Cap Head Screw M6 (Single) (Length: 12mm)
10 | HW1916BC |  |  | Cast 90 Degree Corner Bracket for 3030 - 6 Slot - Black
2 | HW2841BC |  |  | Cast 90 Degree Corner Bracket for 3030 - No tabs / Multi Angle - Black
3 |  |  |  | Countersink Screw M5 (Single) (Length: 25mm)
4 | HW2173SC |  |  | Countersink Screw M6 (Single) (Length: 14mm)
2 | HW2204GC |  |  | Coupler - Spider/Jaw Type - 5mm*8mm
20 | HW1251NC |  |  | Hex Locking Nut - M3
11 | HW1039NC |  |  | Hex Locking Nut - M5
1 |  |  |  | Idler Pulley - Smooth for 2GT-20T - 6mm Belt
2 |  |  |  | Idler Pulley - Smooth for 2GT-20T - 9mm Belt
8 | HW1915PC |  |  | Joining Plate for 3030 - 90 Degree - Black Anodized
2 | HW1588SC |  |  | Lead Screw - TR8*8 Metric Acme Lead Screw - 350mm
3 | HW2036GC |  |  | Linear Rail - MGN12 400mm + MGN12C carriage
2 | HW2035GC |  |  | Linear Rail - MGN12 500mm + 2 x MGN12C carriage
4 | HW1155SC |  |  | Low Profile Screw - 15mm (Single)
6 | HW1630NC |  |  | Mini Precision Shim - 8 x 5 x 1mm
5 | HW1078EC |  |  | Nema 17 Stepper Motor - 48mm - 1.8degree/step, 76oz-in
4 | HW2125GC |  |  | Rubber foot with metal insert - Heavy Duty - 28*22*16.5mm
16 | HW1665NC |  |  | T-Nut - Drop In for 2020 - M3 (Single)
8 | HW1030NC |  |  | T-Nut - Drop In for 2020 - M5 (Single)
68 | HW1821NC |  |  | T-Nut - Drop In for 3030 - M3 (Single)
30 | HW1383NC |  |  | T-Nut - Drop In for 3030 - M5 (Single)
64 | HW1361NC |  |  | T-Nut - Drop In for 3030 - M6 (Single)
2 | HW2118WC |  |  | Thrust Bearing F8-16M
1 | HW1597GC | 1000 |  | Timing Belt - 2GT 6mm (By the meter)
2 | HW1653GC | 2000 |  | Timing Belt - 2GT 9mm (By the meter)
1 | HW1035WC |  |  | Timing Pulley - 2GT (2mm) - 20 Tooth - For 6mm Belt - 5mm Bore
2 | HW1654WC |  |  | Timing Pulley - 2GT (2mm) - 20 Tooth - For 9mm Belt - 5mm Bore
2 |  |  |  | v-cast_x_plate_frame_v1.5
1 |  |  |  | v-cast_x_plate_motor_v1.5
1 |  |  |  | v-cast_y_carriage_v1.5
4 | HW1315NC |  |  | Washer Simple M5
20 | HW1314NC |  |  | Washer Simple M6

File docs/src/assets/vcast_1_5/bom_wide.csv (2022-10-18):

 | SKU |  |  | Product Name
 |  |  |  | Rat Rig V-Cast v1.5
 |  |  |  | 18/10/2022 14:19
 | B.O.M.
QTY | SKU | Length (mm) | Tap | Item Name
4 | HW306BRC | 480 |  | T-SLOT 3030 - Black Anodized 1000mm
3 | HW306BRC | 592 |  | T-SLOT 3030 - Black Anodized 1000mm
2 | HW316BRC | 400 |  | T-SLOT 3060 - Black Anodized 1000mm
1 | HW201BRC | 520 |  | V-SLOT 2020 - Black Anodized 1000mm
6 |  |  |  | Aluminium Spacer - 20mm
5 | HW1019NC |  |  | Aluminium Spacer - 9mm
2 | HW1021GC |  |  | Anti-Backlash Nut Block for 8mm Metric Acme Lead Screw TR8*8
1 | HW2198PC |  |  | Bed Plate - Cast tooling plate - Pre-Machined - 329*329*6mm
8 | HW1336SC |  |  | Button Head Screw M3 (Single) (Length: 8mm)
68 | HW1292SC |  |  | Cap Head Screw M3 (Single) (Length: 12mm)
8 | HW1866SC |  |  | Cap Head Screw M3 (Single) (Length: 18mm)
22 | HW1504SC |  |  | Cap Head Screw M3 (Single) (Length: 20mm)
4 | HW1868SC |  |  | Cap Head Screw M3 (Single) (Length: 35mm)
44 | HW1502SC |  |  | Cap Head Screw M3 (Single) (Length: 8mm)
26 | HW1202SC |  |  | Cap Head Screw M5 (Single) (Length: 12mm)
4 | HW2116SC |  |  | Cap Head Screw M5 (Single) (Length: 14mm)
4 | HW1054SC |  |  | Cap Head Screw M5 (Single) (Length: 20mm)
2 | HW1055SC |  |  | Cap Head Screw M5 (Single) (Length: 25mm)
8 | HW1060SC |  |  | Cap Head Screw M5 (Single) (Length: 35mm)
60 | HW1836SC |  |  | Cap Head Screw M6 (Single) (Length: 12mm)
10 | HW1916BC |  |  | Cast 90 Degree Corner Bracket for 3030 - 6 Slot - Black
2 | HW2841BC |  |  | Cast 90 Degree Corner Bracket for 3030 - No tabs / Multi Angle - Black
3 |  |  |  | Countersink Screw M5 (Single) (Length: 25mm)
4 | HW2173SC |  |  | Countersink Screw M6 (Single) (Length: 14mm)
2 | HW2204GC |  |  | Coupler - Spider/Jaw Type - 5mm*8mm
20 | HW1251NC |  |  | Hex Locking Nut - M3
13 | HW1039NC |  |  | Hex Locking Nut - M5
2 |  |  |  | Idler Pulley - Smooth for 2GT-20T - 6mm Belt
2 |  |  |  | Idler Pulley - Smooth for 2GT-20T - 9mm Belt
8 | HW1915PC |  |  | Joining Plate for 3030 - 90 Degree - Black Anodized
2 | HW1588SC |  |  | Lead Screw - TR8*8 Metric Acme Lead Screw - 350mm
2 | HW2036GC |  |  | Linear Rail - MGN12 400mm + MGN12C carriage
3 | HW2035GC |  |  | Linear Rail - MGN12 500mm + 2 x MGN12C carriage
4 | HW1155SC |  |  | Low Profile Screw - 15mm (Single)
8 | HW1630NC |  |  | Mini Precision Shim - 8 x 5 x 1mm
6 | HW1078EC |  |  | Nema 17 Stepper Motor - 48mm - 1.8degree/step, 76oz-in
4 | HW2125GC |  |  | Rubber foot with metal insert - Heavy Duty - 28*22*16.5mm
20 | HW1665NC |  |  | T-Nut - Drop In for 2020 - M3 (Single)
8 | HW1030NC |  |  | T-Nut - Drop In for 2020 - M5 (Single)
68 | HW1821NC |  |  | T-Nut - Drop In for 3030 - M3 (Single)
30 | HW1383NC |  |  | T-Nut - Drop In for 3030 - M5 (Single)
64 | HW1361NC |  |  | T-Nut - Drop In for 3030 - M6 (Single)
2 | HW2118WC |  |  | Thrust Bearing F8-16M
2 | HW1597GC | 2000 |  | Timing Belt - 2GT 6mm (By the meter)
2 | HW1653GC | 2000 |  | Timing Belt - 2GT 9mm (By the meter)
2 | HW1035WC |  |  | Timing Pulley - 2GT (2mm) - 20 Tooth - For 6mm Belt - 5mm Bore
2 | HW1654WC |  |  | Timing Pulley - 2GT (2mm) - 20 Tooth - For 9mm Belt - 5mm Bore
2 |  |  |  | v-cast_x_plate_frame_v1.5
2 |  |  |  | v-cast_x_plate_motor_v1.5
1 |  |  |  | v-cast_y_carriage_v1.5
8 | HW1315NC |  |  | Washer Simple M5
20 | HW1314NC |  |  | Washer Simple M6

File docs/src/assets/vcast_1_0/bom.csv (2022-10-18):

 | SKU |  |  | Product Name
 |  |  |  | Rat Rig V-Cast v1.0
 |  |  |  | 11/10/2022 14:32
 | B.O.M.
QTY | SKU | Length (mm) | Tap | Item Name
4 | HW306BRC | 480 |  | T-SLOT 3030 - Black Anodized 1000mm
3 | HW306BRC | 492 |  | T-SLOT 3030 - Black Anodized 1000mm
2 | HW316BRC | 400 |  | T-SLOT 3060 - Black Anodized 1000mm
1 | HW201BRC | 420 |  | V-SLOT 2020 - Black Anodized 1000mm
2 | HW1588SC |  |  | 8mm Metric Acme Lead Screw - 350mm
1 | HW1638PC |  |  | Aluminium Bed Plate 329mm * 329mm * 4mm (For 300x300 print area)
2 | HW1021GC |  |  | Anti-Backlash Nut Block for 8mm Metric Acme Lead Screw
14 | HW1336SC |  |  | Button Head Screw M3 (Single) (Length: 8mm)
3 | HW1187SC |  |  | Button Head Screw M5 (Single) (Length: 8mm)
12 | HW1505SC |  |  | Cap Head Screw M3 (Single) (Length: 10mm)
99 | HW1292SC |  |  | Cap Head Screw M3 (Single) (Length: 12mm)
3 | HW1504SC |  |  | Cap Head Screw M3 (Single) (Length: 20mm)
2 | HW1868SC |  |  | Cap Head Screw M3 (Single) (Length: 35mm)
26 | HW1502SC |  |  | Cap Head Screw M3 (Single) (Length: 8mm)
10 | HW1285SC |  |  | Cap Head Screw M5 (Single) (Length: 10mm)
61 | HW1202SC |  |  | Cap Head Screw M5 (Single) (Length: 12mm)
4 | HW2116SC |  |  | Cap Head Screw M5 (Single) (Length: 14mm)
2 | HW1287SC |  |  | Cap Head Screw M5 (Single) (Length: 16mm)
1 | HW1054SC |  |  | Cap Head Screw M5 (Single) (Length: 20mm)
1 | HW1055SC |  |  | Cap Head Screw M5 (Single) (Length: 25mm)
2 | HW1058SC |  |  | Cap Head Screw M5 (Single) (Length: 30mm)
73 | HW1836SC |  |  | Cap Head Screw M6 (Single) (Length: 12mm)
2 | HW1636BC |  |  | Cast 90 Degree Corner Bracket for 2020 - 20mm x 30mm - Black
10 | HW1916BC |  |  | Cast 90 Degree Corner Bracket for 3030 - 6 Slot - Black
2 | HW1001GC |  |  | Flexible Coupling - 5mm x 8mm
12 | HW1819NC |  |  | Hex Locking Nut - M3 Black
7 | HW1039NC |  |  | Hex Locking Nut - M5
2 | HW1508NC |  |  | Hex Nut - M3
1 | HW2058WC |  |  | Idler Pulley - Smooth for GT2-20T - 9mm Belt - 5mm Bore (standard)
8 | HW1915PC |  |  | Joining Plate for 3030 - 90 Degree - Black Anodized
2 | HW2036GC |  |  | Linear Rail - MGN12 400mm + MGN12C carriage
1 | HW2035GC |  |  | Linear Rail - MGN12 500mm + 2 x MGN12C carriage
1 | HW2034GC |  |  | Linear Rail - MGN12 500mm + MGN12C carriage
1 | HW2033GC |  |  | Linear Rail - MGN15 360mm + MGN15C carriage
4 | HW1155SC |  |  | Low Profile Screw - 15mm (Single)
4 | HW1157SC |  |  | Low Profile Screw - 25mm (Single)
2 | HW1072WC |  |  | Mini Ball Bearing 5 x 10 x 4.2 - MR105ZZ
6 | HW1630NC |  |  | Mini Precision Shim - 8 x 5 x 1mm - C
1 | HW2078WC |  |  | Rat Rig 6mm Custom Smooth Idler Pulley (compressible)
4 | HW2125GC |  |  | Rubber foot with metal insert - Heavy Duty - 28*22*16.5mm
4 | HW1591GC |  |  | Spring - Steel
15 | HW1665NC |  |  | T-Nut - Drop In for 2020 - M3 (Single)
12 | HW1030NC |  |  | T-Nut - Drop In for 2020 - M5 (Single)
80 | HW1821NC |  |  | T-Nut - Drop In for 3030 - M3 (Single)
81 | HW1383NC |  |  | T-Nut - Drop In for 3030 - M5 (Single)
73 | HW1361NC |  |  | T-Nut - Drop In for 3030 - M6 (Single)
1 | HW1597GC | 1300 |  | Timing Belt - GT2 6mm (By the meter)
1 | HW1653GC | 1200 |  | Timing Belt - GT2 9mm (By the meter)
1 | HW1035WC |  |  | Timing Pulley - GT2 (2mm) - 20 Tooth
1 | HW1654WC |  |  | Timing Pulley - GT2 (2mm) - 20 Tooth - For 9mm Belt
1 | HW2070PC |  |  | V-CAST_Y_Plate_Bed_Carriage_v0.6
24 | HW1314NC |  |  | Washer Simple M6

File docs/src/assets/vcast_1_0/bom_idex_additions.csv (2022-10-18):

 | SKU |  |  | Product Name
 |  |  |  | Rat Rig V-Cast v1.0 IDEX Additions
 |  |  |  | 11/10/2022 14:32
 | B.O.M.
QTY | SKU | Length (mm) | Tap | Item Name
1 | HW1019NC |  |  | Aluminium Spacer - 9mm
8 | HW1336SC |  |  | Button Head Screw M3 (Single) (Length: 8mm)
1 | HW1058SC |  |  | Cap Head Screw M5 (Single) (Length: 30mm)
3 | HW1836SC |  |  | Cap Head Screw M6 (Single) (Length: 12mm)
1 | HW2073GC |  |  | Linear Rail - MGN15C Carriage Only
2 | HW1072WC |  |  | Mini Ball Bearing 5 x 10 x 4.2 - MR105ZZ
4 | HW1630NC |  |  | Mini Precision Shim - 8 x 5 x 1mm - C
1 | HW2078WC |  |  | Rat Rig 6mm Custom Smooth Idler Pulley (compressible)
3 | HW1361NC |  |  | T-Nut - Drop In for 3030 - M6 (Single)
1 | HW1597GC | 1300 |  | Timing Belt - GT2 6mm (By the meter)
1 | HW1035WC |  |  | Timing Pulley - GT2 (2mm) - 20 Tooth
2 | HW2071PC |  |  | V-CAST_X_Plate_Motor_v0.6

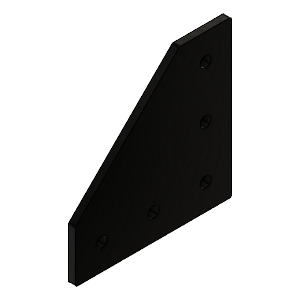
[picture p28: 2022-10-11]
docs/src/cad/components/HW1915PC-Joining Plate for 3030 - 90 Degree - Black Anodized.png

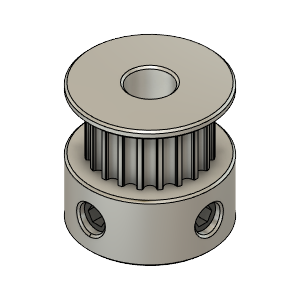
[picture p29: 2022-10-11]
docs/src/cad/components/HW1035WC-Timing Pulley - 2GT-20T - For 6mm Belt - 5mm Bore.png

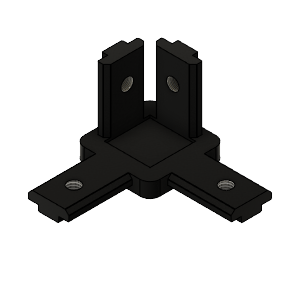
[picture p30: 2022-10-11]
docs/src/cad/components/HW1832BC-Inside Hidden Three Way Corner - Black - 3030.png

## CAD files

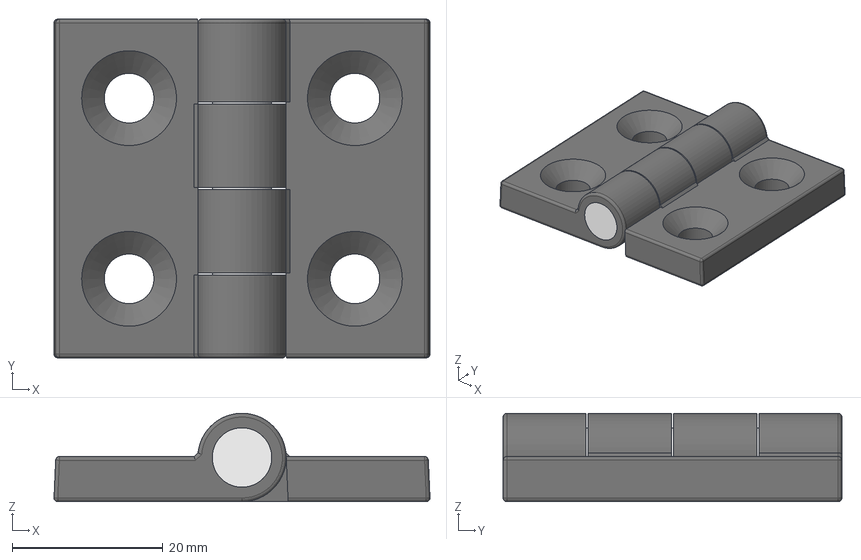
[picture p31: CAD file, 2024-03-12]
docs/src/cad/components/HW1848GC-Hinge - Black thermoplastic - for 3030 - 45mm Length.step
50.0 x 45.0 x 11.7 mm
_Hinge Left
_Hinge Right
HW1848GC_1

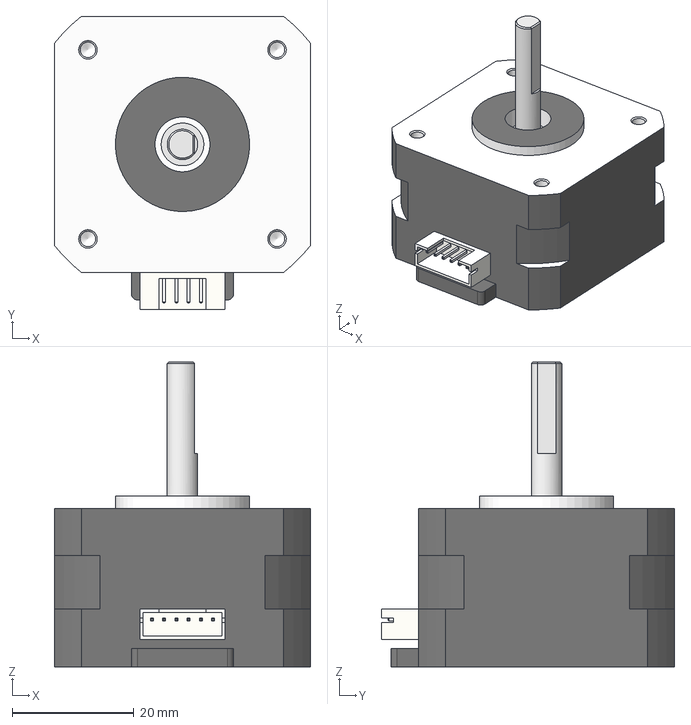
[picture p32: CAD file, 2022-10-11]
docs/src/cad/electronics/HW1833EC-Nema 17 Stepper Motor - 25mm - 0.9deg.step
42.0 x 48.1 x 50.0 mm

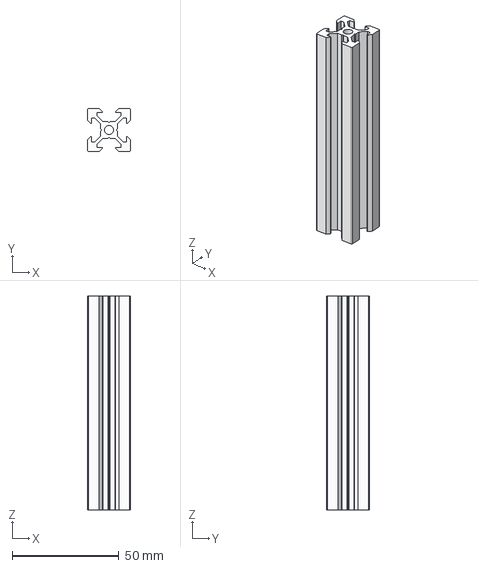
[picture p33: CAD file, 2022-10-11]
docs/src/cad/extrusions/20_series/HW204NRC-V-SLOT 2020 - Natural Anodized.step
20.0 x 20.0 x 100.0 mm

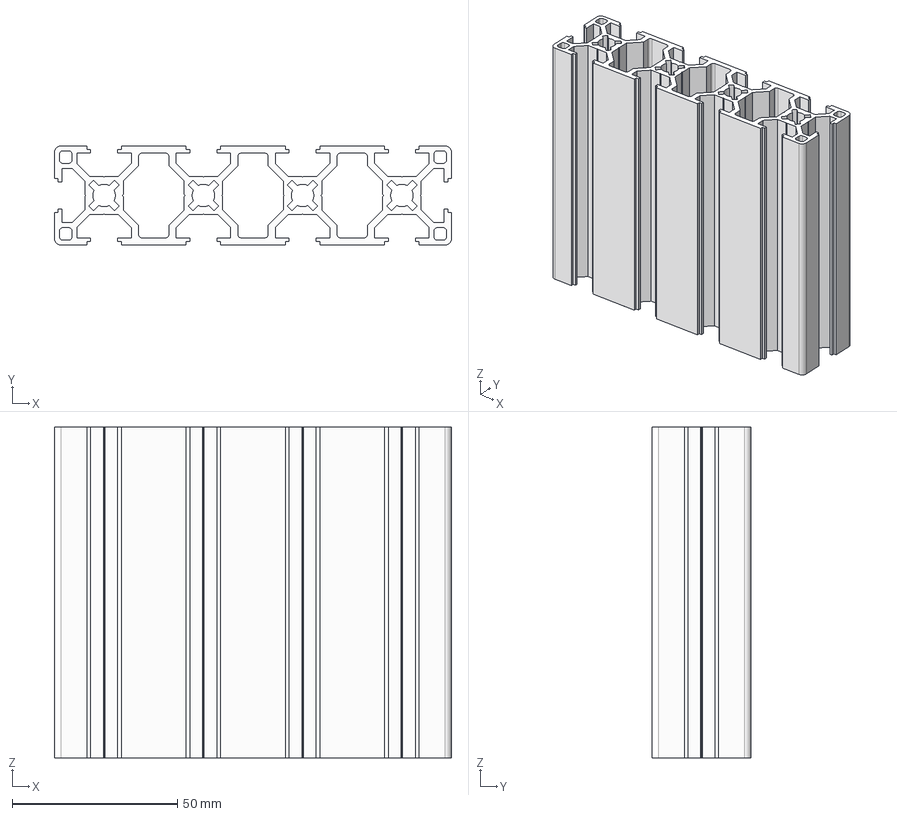
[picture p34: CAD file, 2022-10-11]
docs/src/cad/extrusions/30_series/HW332NRC-T-SLOT 30120 - Natural Anodized.step
120.0 x 30.0 x 100.0 mm

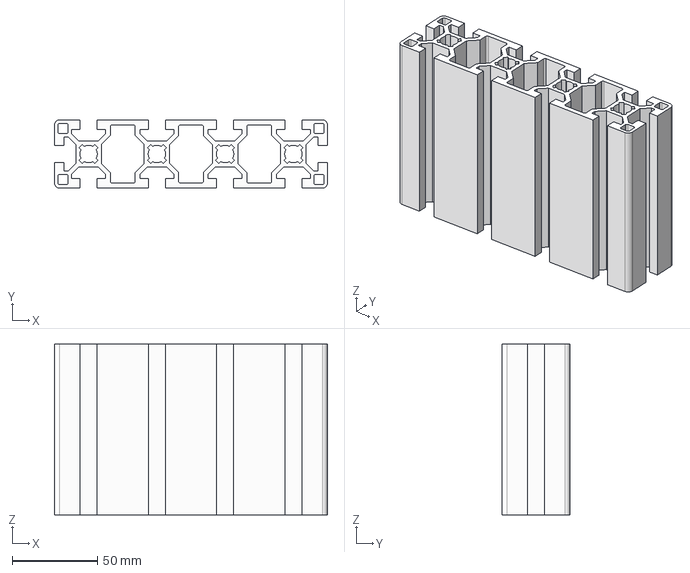
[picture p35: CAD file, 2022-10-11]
docs/src/cad/extrusions/40_series/HW436NRC-T-SLOT 40160 - Natural Anodized.step
160.0 x 40.0 x 100.0 mm

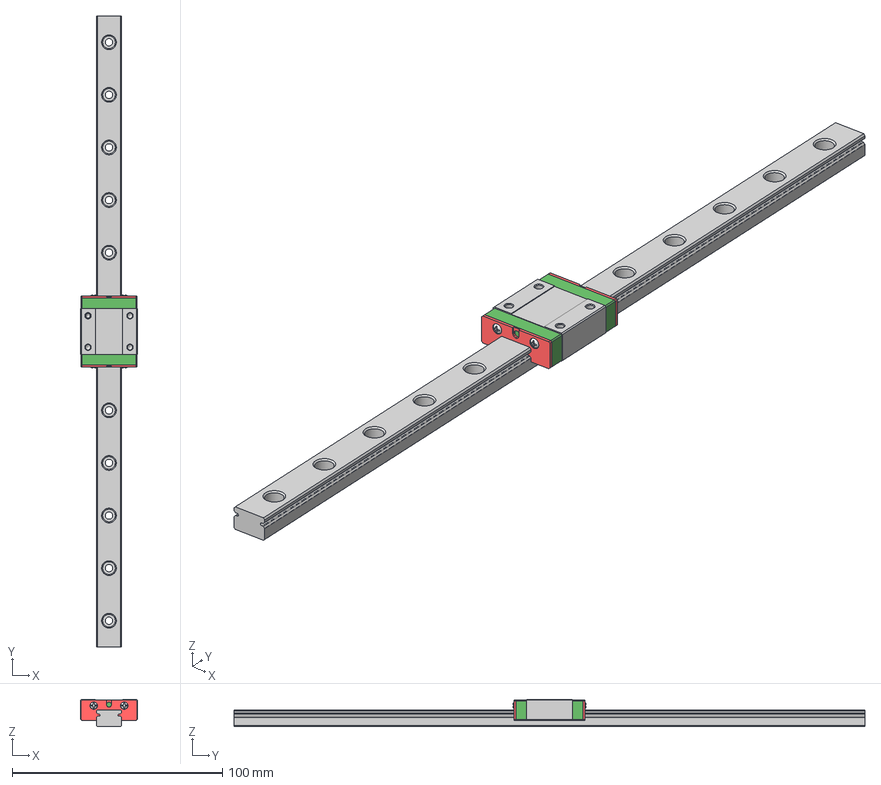
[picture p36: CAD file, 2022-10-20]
docs/src/cad/linear_rails/mgn12/HW2911GC-Linear Rail - MGN12 300mm + MGN12C carriage.step
27.0 x 300.0 x 13.0 mm

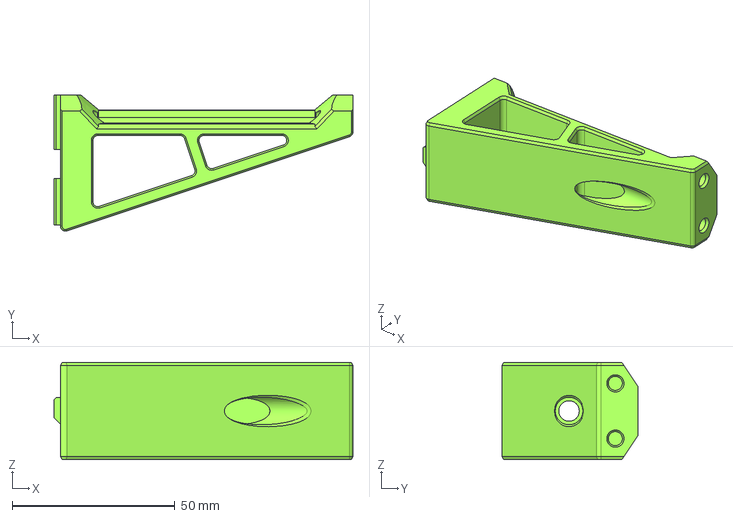
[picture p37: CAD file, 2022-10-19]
docs/src/cad/official_models/3030_spool_holder.step
92.0 x 41.9 x 30.0 mm

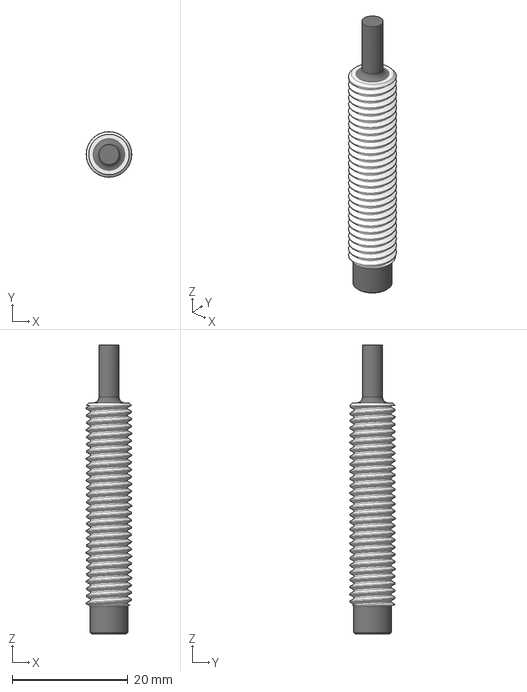
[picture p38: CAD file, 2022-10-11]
docs/src/cad/electronics/HW2901EC-Rat Rig SuperPinda Probe by P&F.step
7.88 x 7.88 x 50.0 mm

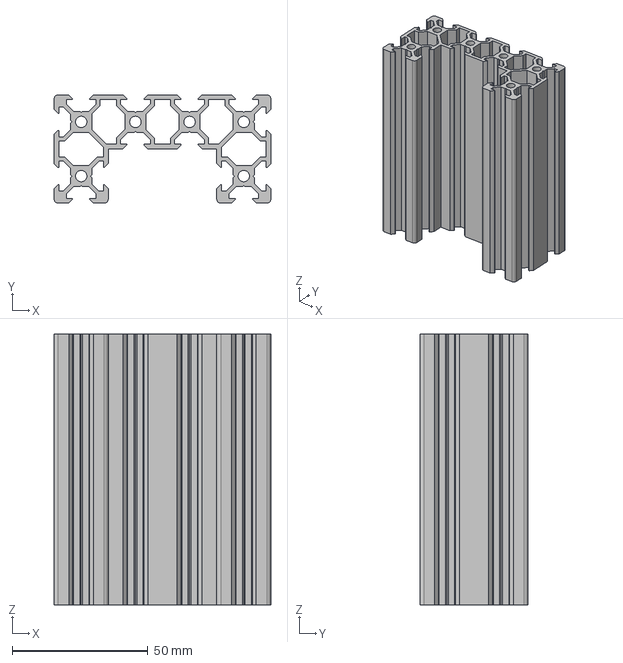
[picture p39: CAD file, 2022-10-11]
docs/src/cad/extrusions/20_series/HW901BRC-C-BEAM - Black Anodized.step
80.0 x 40.0 x 100.0 mm

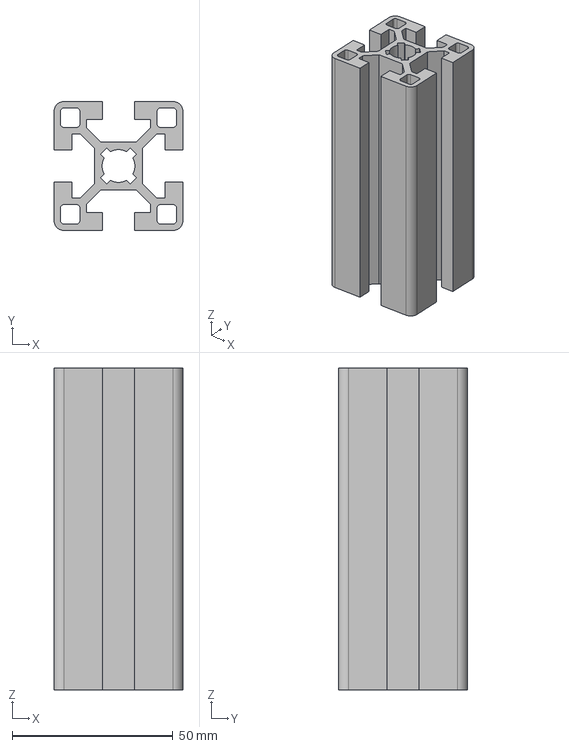
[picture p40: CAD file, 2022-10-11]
docs/src/cad/extrusions/40_series/HW441BRC-T-SLOT 4040 - Black Anodized.step
40.0 x 40.0 x 100.0 mm

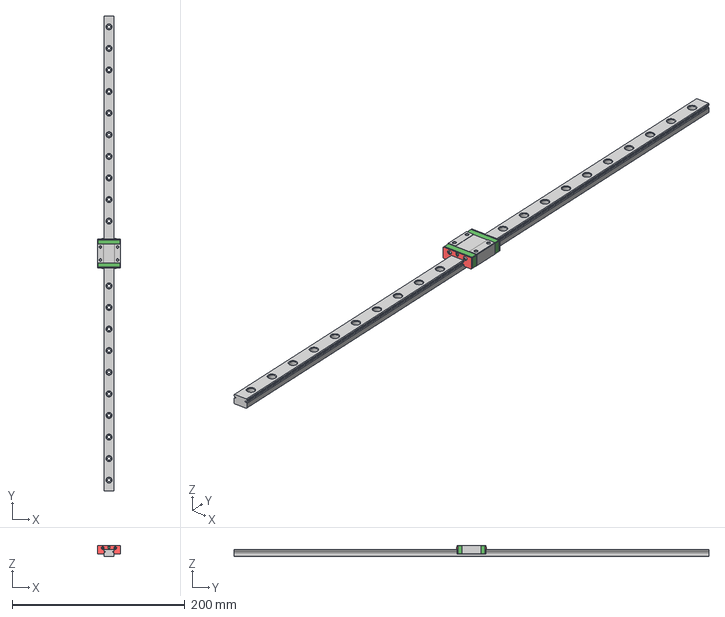
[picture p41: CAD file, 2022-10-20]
docs/src/cad/linear_rails/mgn12/HW2355GC-Linear Rail - MGN12 550mm + MGN12C carriage.step
27.0 x 550.0 x 13.0 mm

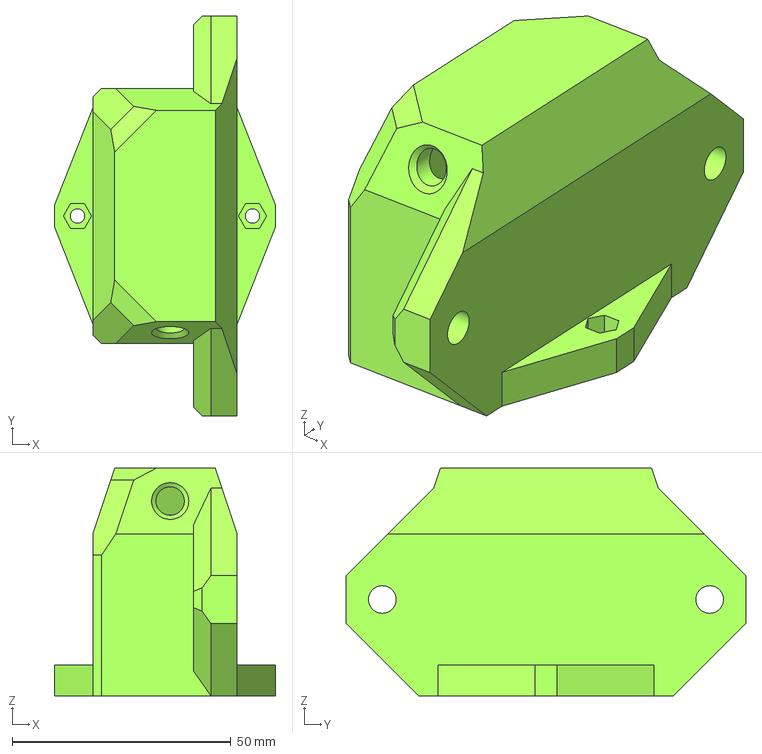
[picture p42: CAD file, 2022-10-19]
docs/src/cad/official_models/3030_iec_mount.step
50.5 x 91.3 x 52.0 mm

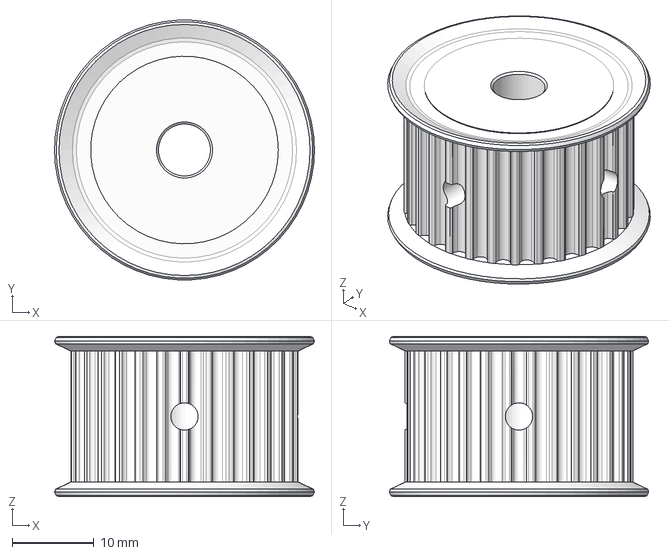
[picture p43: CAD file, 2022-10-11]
docs/src/cad/components/HW2980WC-HTD3M 15mm Belt Pulley 30T 6.35mm Bore.step
31.8 x 31.7 x 19.6 mm

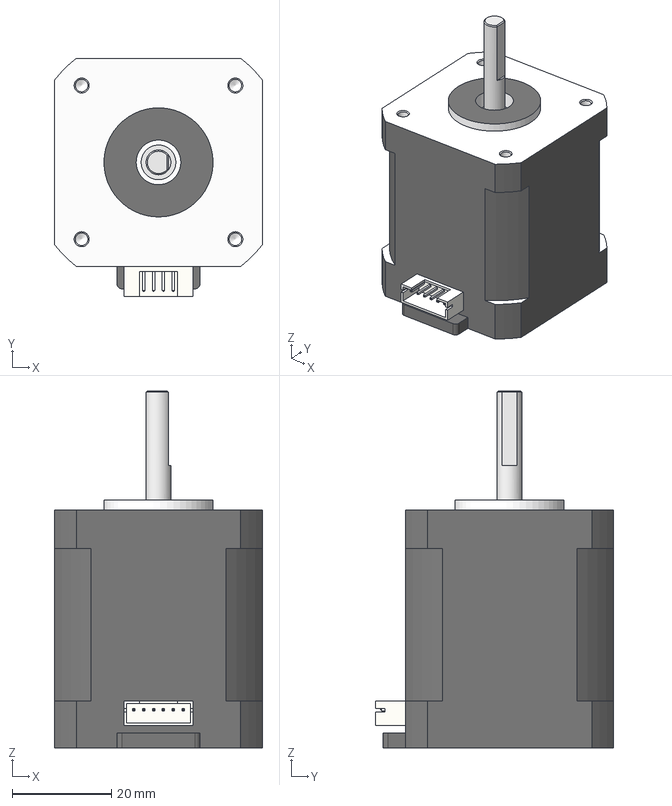
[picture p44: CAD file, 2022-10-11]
docs/src/cad/electronics/HW1078EC-Nema 17 Stepper Motor - 48mm - 1.8degree, 76oz-in.step
42.0 x 48.1 x 72.0 mm

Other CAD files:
docs/src/cad/extrusions/30_series/HW336BRC-T-SLOT 30120 - Black Anodized.step
docs/src/cad/extrusions/20_series/HW601NRC-V-SLOT 2060 - Natural Anodized.step
docs/src/cad/extrusions/30_series/HW326BRC-T-SLOT 3090 - Black Anodized.step
docs/src/cad/extrusions/40_series/HW431BRC-T-SLOT 40160 - Black Anodized.step
docs/src/cad/components/HW1016NC-Aluminium Spacer - 3mm.step
docs/src/cad/components/HW1018NC-Aluminium Spacer - 6mm.step
docs/src/cad/components/HW1019NC-Aluminium Spacer - 9mm.step
docs/src/cad/components/HW1035WC-Timing Pulley - 2GT-20T - For 6mm Belt - 5mm Bore.step
docs/src/cad/components/HW1305BC-Inside Hidden Corner Bracket - for 3030.step
docs/src/cad/components/HW1309WC-Ball Bearing - F688ZZ.step
docs/src/cad/components/HW1555GC-V-Slot Door Handle.step
docs/src/cad/components/HW1630NC-Mini Precision Shim - 8x5x1mm.step
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

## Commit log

2022-10-11 Initial CAD data import
    [HW1016NC-Aluminium Spacer - 3mm.step, HW1018NC-Aluminium Spacer - 6mm.step, HW1019NC-Aluminium Spacer - 9mm.step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]
2022-10-18 Add V-Core 3.1 IDEX data
    [bom.csv, printed_parts.csv]
2022-10-18 Add V-Core 3.1 IDEX "Wide Boy" data
    [bom.csv, printed_parts.csv]
2022-10-18 Add V-Cast v1.0 data
    [bom.csv, bom_idex_additions.csv, bom_wide.csv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]
2022-10-18 Add V-Cast v1.5 data
    [bom.csv, bom_wide.csv, printed_parts.csv]
2022-10-19 Add VC3.1 Beast Enclosure data
    [bom.csv, printed_parts.csv]
2022-10-19 Add official mods data
    [3030_iec_mount.step, 3030_iec_mount.stl, 3030_spool_holder.step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]
2022-10-19 Update plugin, add support for an STL repo
2022-10-20 Add MGN12 linear rails to CAD library
    [HW2034GC-Linear Rail - MGN12 500mm + MGN12C carriage.step, HW2036GC-Linear Rail - MGN12 400mm + MGN12C carriage.step, HW2036GC-Linear Rail - MGN12 450mm + MGN1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]
2022-10-21 Remove Material Insiders from ci/cd
2022-10-24 Fix minor BOM error on both VC3.1 IDEX
    [bom.csv]
2022-10-25 Add IDEX Motor Plate SKU to IDEX BOMs
    [bom.csv]
2024-03-12 Add HW1848GC - 3030 Hinge to CAD library
    [HW1848GC-Hinge - Black thermoplastic - for 3030 - 45mm Length.step]
2024-10-29 Add V-Minion 1.1 non-toolboard toolhead
